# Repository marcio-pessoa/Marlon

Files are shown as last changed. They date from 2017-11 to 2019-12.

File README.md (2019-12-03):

# Marlon Mark I - 3D Printer

## Introduction

Marlon is a Marlin firmware based 3D Printer. It uses RepRap concept with RAMPS.

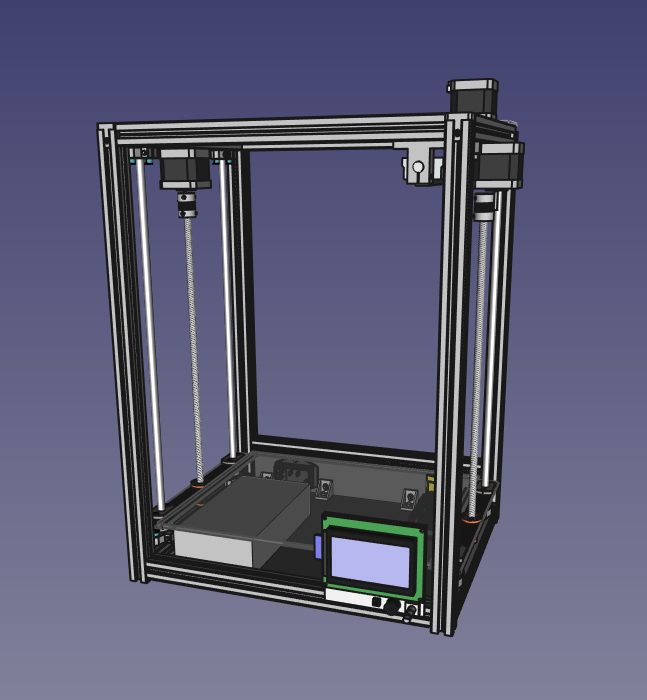
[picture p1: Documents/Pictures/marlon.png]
Marlon


## Cloning
```
git clone --recurse-submodules https://github.com/marcio-pessoa/Marlon.git
```

<!---
Work area:

Width: ??? mm
Height: ??? mm
Depth: ??? mm

## Videos
Watch this projects videos on [YouTube Playlist].
--->

## Changes
All notable changes to this project will be documented in this [Change log](CHANGELOG.md).

## Mechanics
This project uses an original mech made from scratch with the following goals:
- Reliable
- Precise
- Robust
- Well done
- Almost cheap, but very beautiful

Check out [Mechanics](Mechanics/README.md) design to know more.

## Electronics
Arduino, RAMPS and Full Graphic Smart Controller are used to [Electronics](Electronics/README.md) control system.

## Firmware
Marlin is my [Firmware](Firmware/README.md)! :-)

## Software
A lot of softwares can be used to draw 3D objects, slice, convert to G-code and print. Here are [some recommended softwares](Software/README.md).

## BOM - Bill of materials
If you want to build your own, take a look at [Bill of materials](BOM.md).

---

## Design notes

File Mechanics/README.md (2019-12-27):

# Marlon Mark I - 3D Printer

[Main page]

## Mechanics

### Frame
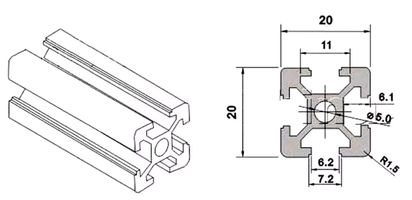
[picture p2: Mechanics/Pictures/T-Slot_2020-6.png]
T-Slot 2020-6


Technical specifications:
- Frame type: T-Slot 2020-6
- Width: 337 mm
- Height: 445 mm
- Depth: 287 mm

#### Hinges
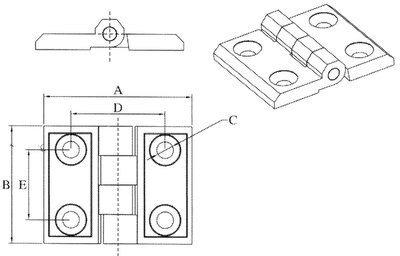
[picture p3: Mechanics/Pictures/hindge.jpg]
T-Slot 2020 Hinge


T-Slot 2020 Hinge

Technical specifications:
- Frame type: T-Slot 2020-6
- A:  mm
- B:  mm
- C:  mm
- D:  mm
- E:  mm

#### Round Roll T-Nut for T-slot 2020

##### M3
Technical specifications:
- Material: Nickel Plated
- Shaft: 3mm

##### M4
Technical specifications:
- Material: Nickel Plated
- Shaft: 4mm

##### M5
Technical specifications:
- Material: Nickel Plated
- Shaft: 5mm

### CoreXY
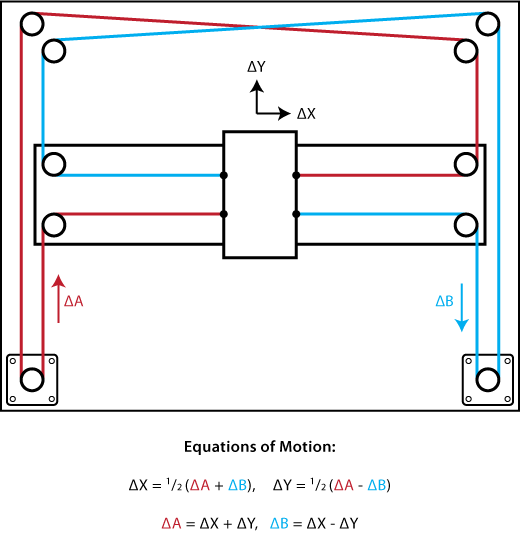
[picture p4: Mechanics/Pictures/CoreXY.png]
CoreXY


The [CoreXY] is a open source two-axis linear motion implementation developed at MIT Media Lab.

Overall, it delivers the same benefit of the H-bot, a light moving platform, by keeping both motors fixed to the frame. Furthermore, by crossing the belt, the unwanted torque vectors of H-bot model are eliminated.

#### SC8LUU
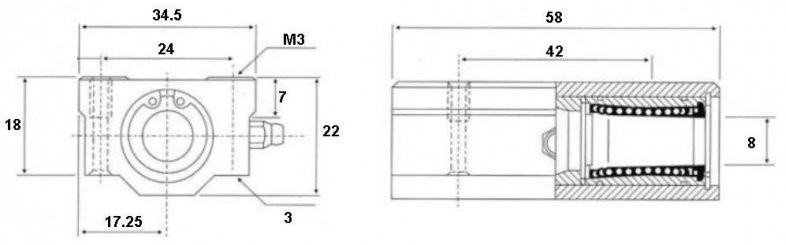
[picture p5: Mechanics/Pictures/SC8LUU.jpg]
SC8LUU


Technical specifications:

#### Linear rod
Technical specifications:
- Diameter: 8 mm
- Lenght: 300 mm
- Material: Carbon Steel

#### Pulley
Technical specifications:
- Timing: 20T
- Bore: 5mm
- Belt: GT2 6 mm

#### Belt
Technical specifications:
- Standard: GT2
- Pinch: 2 mm
- Wide: 6 mm
- Lenght: <span style="color:#F00">???</span> mm

### Elevator (z axis)

#### Base
Technical specifications:
- Material: Celeron

#### LMH8UU
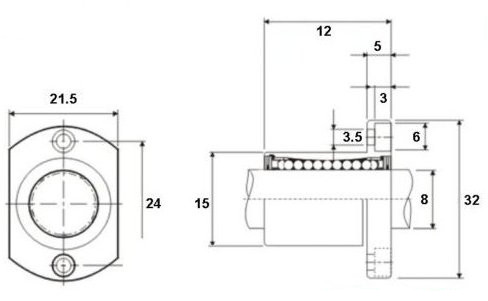
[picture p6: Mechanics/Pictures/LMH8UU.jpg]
LMH8UU


#### SHF
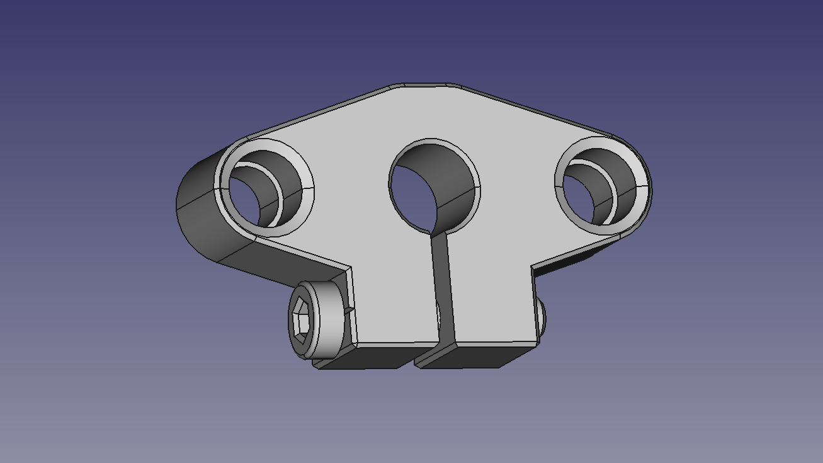
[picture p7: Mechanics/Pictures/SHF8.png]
SHF


Technical specifications:

#### Shaft coupler
Technical specifications:
- Diameter: 19 mm
- Lenght: 25 mm
- Material: Aluminium
- Net weight: 16 g
- Shaft: 5 -> 8 mm

#### Threaded rod
Technical specifications:
- Material: 304 Stainless Steel
- Diameter: 8 mm
- Pitch: 2 mm
- Lead: 4
- Length: 400 mm

#### T8
Technical specifications:
- Material: Brass
- Big nut diameter: 30mm
- Thickness: 5mm
- Small nut diameter: 16mm
- Feature: anti-backlash

#### Linear rail
Technical specifications:
- Diameter: 8 mm
- Lenght: 400 mm
- Material: Carbon Steel

[Main page]

---

[Celeron TechSpecs]: dados-tecnicos-celeron.pdf
[Main page]: ../README.md
[CoreXY]: http://corexy.com/

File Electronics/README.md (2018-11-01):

# Marlon Mark I - 3D Printer

[Main page]

## Electronics

### Power
Technical specifications:
https://www.stayonline.com/5-15-c13-10-amp-power-cords.aspx

- N: neutro (black)
- F: fase (white)
- T: ground (green)

#### Power connector

             T        
          +------+    
         /   ▉▉   \   
        +          +  
        | ▉▉    ▉▉ |  
        +----------+  
          F      N    

Technical specifications:
- Standard: IEC 60320
- Coupler: C13

#### Power supply
Technical specifications:
- Model: PMC-12V150W1BA
- Technology: Switching power supply
- Input:
  - Voltage: 100 ~ 240 VAC
  - Amperage: 2 A
  - Frequency: 50 ~ 60 Hz
  - Power: 150 W
- Output 1: 
  - Voltage: 12 VDC
  - Amperage: 12.6 A

### Arduino
Technical specifications:
- Model: [Arduino Mega 2560]

#### Diagram
                                 .-----.                                        
    .----[PWR]-------------------| USB |--.                                     
    |                            '-----'  |                                     
    |           GND/RST2  [ ] [ ]         |                                     
    |         MOSI2/SCK2  [ ] [ ]  SCL[ ] |   D0                                
    |            5V/MISO2 [ ] [ ]  SDA[ ] |   D1                                
    |                             AREF[ ] |                                     
    |                              GND[ ] |                                     
    | [ ]NC                     SCK/13[ ]~|   B7                                
    | [ ]v.ref                 MISO/12[ ]~|   B6                                
    | [ ]RST                   MOSI/11[ ]~|   B5                                
    | [ ]3V3      +----------+      10[ ]~|   B4                                
    | [ ]5v       | ARDUINO  |       9[ ]~|   H6                                
    | [ ]GND      |   MEGA   |       8[ ]~|   H5                                
    | [ ]GND      +----------+            |                                     
    | [ ]Vin                         7[ ]~|   H4                                
    |                                6[ ]~|   H3                                
    | [ ]A0                          5[ ]~|   E3                                
    | [ ]A1                          4[ ]~|   G5                                
    | [ ]A2                     INT5/3[ ]~|   E5                                
    | [ ]A3                     INT4/2[ ]~|   E4                                
    | [ ]A4                       TX>1[ ]~|   E1                                
    | [ ]A5                       RX<0[ ]~|   E0                                
    | [ ]A6                               |                                     
    | [ ]A7                     TX3/14[ ] |   J1                                
    |                           RX3/15[ ] |   J0                                
    | [ ]A8                     TX2/16[ ] |   H1                                
    | [ ]A9                     RX2/17[ ] |   H0                                
    | [ ]A10               TX1/INT3/18[ ] |   D3                                
    | [ ]A11               RX1/INT2/19[ ] |   D2                                
    | [ ]A12           I2C-SDA/INT1/20[ ] |   D1                                
    | [ ]A13           I2C-SCL/INT0/21[ ] |   D0                                
    | [ ]A14                              |                                     
    | [ ]A15                              |   PORTS                             
    |                RST SCK MISO         |    22=A0  23=A1                     
    |         ICSP   [ ] [ ] [ ]          |    24=A2  25=A3                     
    |                [ ] [ ] [ ]          |    26=A4  27=A5                     
    |                GND MOSI 5V          |    28=A6  29=A7                     
    | G                                   |    30=C7  31=C6                     
    | N 5 5 4 4 4 4 4 3 3 3 3 3 2 2 2 2 5 |    32=C5  33=C4                     
    | D 2 0 8 6 4 2 0 8 6 4 2 0 8 6 4 2 V |    34=C3  35=C2                     
    |         ~ ~                         |    36=C1  37=C0                     
    | @ # # # # # # # # # # # # # # # # @ |    38=D7  39=G2                     
    | @ # # # # # # # # # # # # # # # # @ |    40=G1  41=G0                     
    |           ~                         |    42=L7  43=L6                     
    | G 5 5 4 4 4 4 4 3 3 3 3 3 2 2 2 2 5 |    44=L5  45=L4                     
    | N 3 1 9 7 5 3 1 9 7 5 3 1 9 7 5 3 V |    46=L3  47=L2                     
    | D                                   |    48=L1  49=L0    SPI:             
    |                                     |    50=B3  51=B2     50=MISO 51=MOSI
    |     2560                            |    52=B1  53=B0     52=SCK  53=SS   
    '--.                         .--------'                                     
        \_______________________/                                               

Diagram by: http://busyducks.com/ascii-art-arduinos

#### Pin designation
 id | pin |   type    | direction |               description                
----|-----|-----------|-----------|--------------------------------------------
  0 |   0 | -         | -         | -                                        
  1 |   1 | -         | -         | -                                        
  2 |   2 | -         | -         | X_MAX_PIN                                
  3 |   3 | -         | -         | X_MIN_PIN                                
  4 |   4 | -         | -         | -                                        
  5 |   5 | -         | -         | -                                        
  6 |   6 | -         | -         | -                                        
  7 |   7 | -         | -         | -                                        
  8 |   8 | -         | -         | HEATER_1_PIN                             
  9 |   9 | -         | -         | FAN_PIN                                  
 10 |  10 | -         | -         | HEATER_0_PIN                             
 11 |  11 | -         | -         | -                                        
 12 |  12 | -         | -         | PS_ON_PIN                                
 13 |  13 | -         | -         | LED_PIN                                  
 14 |  14 | -         | -         | Y_MIN_PIN                                
 15 |  15 | -         | -         | Y_MAX_PIN                                
 16 |  16 | -         | -         | -                                        
 17 |  17 | -         | -         | -                                        
 18 |  18 | -         | -         | Z_MIN_PIN                                
 19 |   4 | -         | -         | Z_MAX_PIN                                
 20 |  20 | -         | -         | -                                        
 21 |  21 | -         | -         | -                                        
 22 |  22 | -         | -         | -                                        
 23 |  23 | -         | -         | -                                        
 24 |  24 | -         | -         | E_ENABLE_PIN                             
 25 |  25 | -         | -         | -                                        
 26 |  26 | -         | -         | E_STEP_PIN                               
 27 |  27 | -         | -         | -                                        
 28 |  28 | -         | -         | E_DIR_PIN                                
 29 |  29 | -         | -         | -                                        
 30 |  30 | -         | -         | -                                        
 31 |  31 | -         | -         | -                                        
 32 |  32 | -         | -         | -                                        
 33 |  33 | -         | -         | -                                        
 34 |  34 | -         | -         | -                                        
 35 |  35 | -         | -         | -                                        
 36 |  36 | -         | -         | -                                        
 37 |  37 | -         | -         | -                                        
 38 |  38 | -         | -         | X_ENABLE_PIN                             
 39 |  39 | -         | -         | -                                        
 40 |  40 | -         | -         | -                                        
 41 |  41 | -         | -         | -                                        
 42 |  42 | -         | -         | -                                        
 43 |  43 | -         | -         | -                                        
 44 |  44 | -         | -         | -                                        
 45 |  45 | -         | -         | -                                        
 46 |  46 | -         | -         | Z_STEP_PIN                               
 47 |  47 | -         | -         | -                                        
 48 |  48 | -         | -         | Z_DIR_PIN                                
 49 |  49 | -         | -         | -                                        
 50 |  50 | -         | -         | -                                        
 51 |  51 | -         | -         | -                                        
 52 |  52 | -         | -         | -                                        
 53 |  53 | -         | -         | SDSS                                     
 54 |   0 | -         | -         | X_STEP_PIN                               
 55 |   1 | -         | -         | X_DIR_PIN                                
 56 |   2 | -         | -         | Y_ENABLE_PIN                             
 57 |   3 | -         | -         | -                                        
 58 |   4 | -         | -         | -                                        
 59 |   5 | -         | -         | -                                        
 60 |   6 | -         | -         | Y_STEP_PIN                               
 61 |   7 | -         | -         | Y_DIR_PIN                                
 62 |   8 | -         | -         | Z_ENABLE_PIN                             
 63 |   9 | -         | -         | -                                        
 64 |  10 | -         | -         | -                                        
 65 |  11 | -         | -         | -                                        
 66 |  12 | -         | -         | -                                        
 67 |  13 | -         | -         | TEMP_0_PIN                               
 68 |  14 | -         | -         | TEMP_1_PIN                               
 69 |  15 | -         | -         | -                                        

### RAMPS
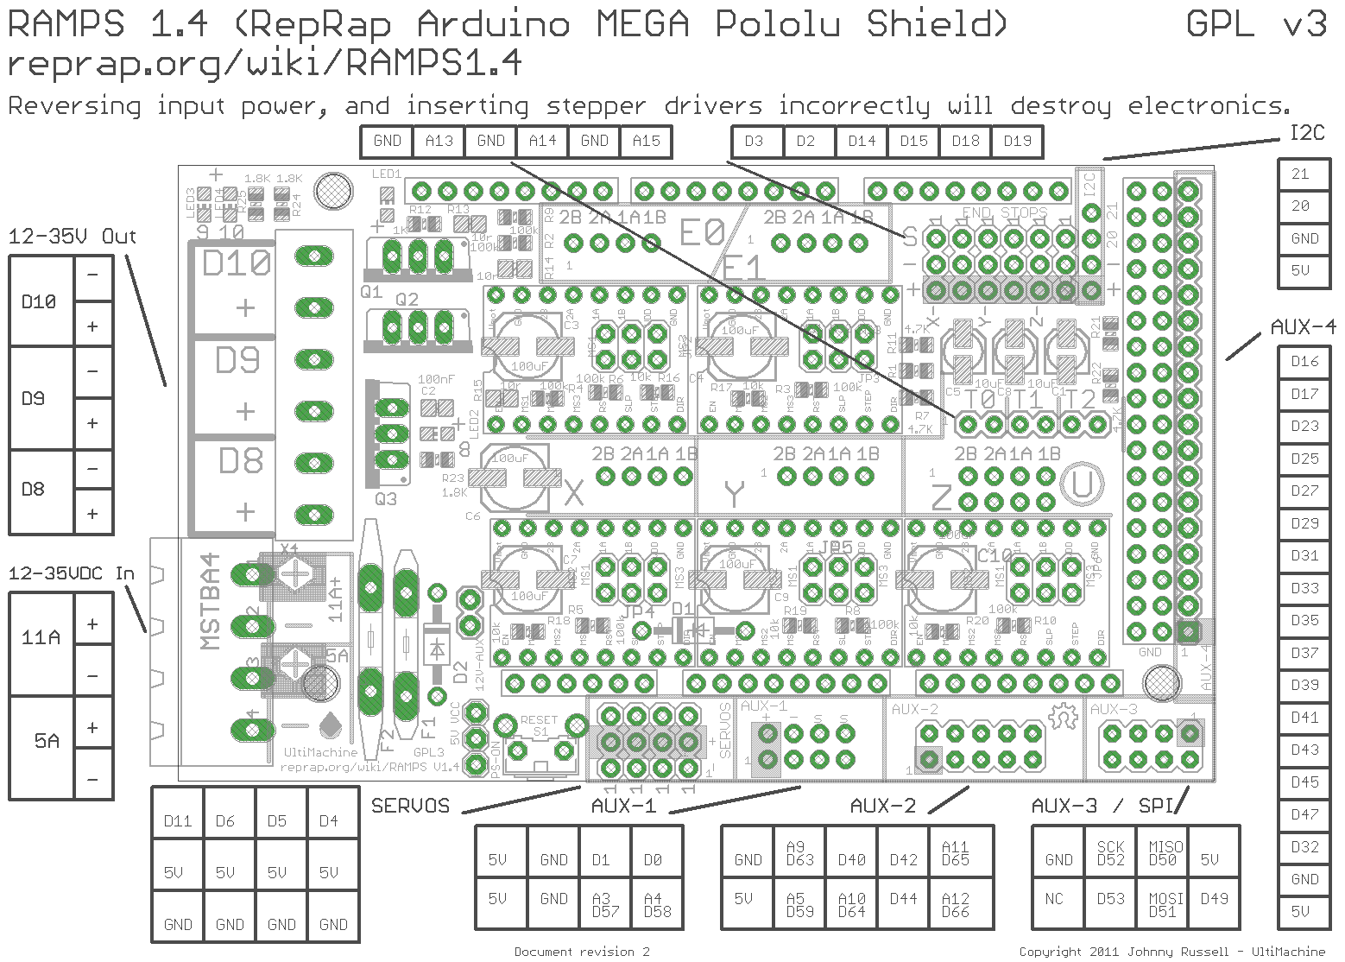
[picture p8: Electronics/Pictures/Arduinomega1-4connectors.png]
RAMPS 1.4


> RepRap Arduino Mega Pololu Shield, or RAMPS for short. It is designed to fit the entire electronics needed for a RepRap in one small package for low cost. RAMPS interfaces an Arduino Mega with the powerful Arduino MEGA platform and has plenty room for expansion. The modular design includes plug in stepper drivers and extruder control electronics on an Arduino MEGA shield for easy service, part replacement, upgrade-ability and expansion. Additionally, a number of Arduino expansion boards can be added to the system as long as the main RAMPS board is kept to the top of the stack.
>
> -- From: [RAMPS]

Technical specifications:
- Version: 1.4
- License: GPL

### Display
Technical specifications:
- Model: [Full Graphic Smart Controller]
- Resolution: 128 x 64 pixels
- Technology: LCD
- License: GPL
- Author: RepRapDiscount.com

### Stepper drivers
Technical specifications:
- Model: A4988

Each driver has and heat sink to 

RAMPS has 3 jumpers to configure each axes resolution.
That can be set to configure the motor microstepping.

#### Resolution configuration

##### Pololu A4988
 M0   | M1   | M2   | Microstep resolution
------|------|------|-----------------------
 Low  | Low  | Low  | Full step
 High | Low  | Low  | Half step
 Low  | High | Low  | Quarter step
 High | High | Low  | Eighth step
 High | High | High | Sixteenth step

##### Pololu DRV8825
 M0   | M1   | M2   | Microstep resolution
------|------|------|-----------------------
 Low  | Low  | Low  | Full step
 High | Low  | Low  | Half step
 Low  | High | Low  | 1/4 step
 High | High | Low  | 1/8 step
 Low  | Low  | High | 1/16 step
 High | Low  | High | 1/32 step
 Low  | High | High | 1/32 step
 High | High | High | 1/32 step

### Stepper motor
Technical specifications:
- Model: 42BYGHM809
- Holding Torque: 48 N·cm
- Rated voltage: 3.06 V
- Shaft: Ø 5 mm no flat
- Step angle: 0.9 degree
- Motor length: 48 mm
- Rated current: 1.7 A/phase
- Inductance: 2.8 mH
- Frame Size: NEMA17
- Step Angle:                    0.9 degree
- Wires: 4
- Weight: 0.34 kg
- Length: 48 mm
- Motor shaft : 5mm
- Front shaft length: 20mm

<!---
- Voltage: 2.8V
- Resistance: 1.65Ohm/phase
- Inductance: 4.0mH/phase
- Holding torque: 4200g.cm 60oz-in
- Rotor inertia: 68g-cm2
- Detent torque: 0.22g-cm
--->

Stepper motor [reference](http://reprap.org/wiki/NEMA_17_Stepper_motor).

### Hot bed

### Endstop sensor
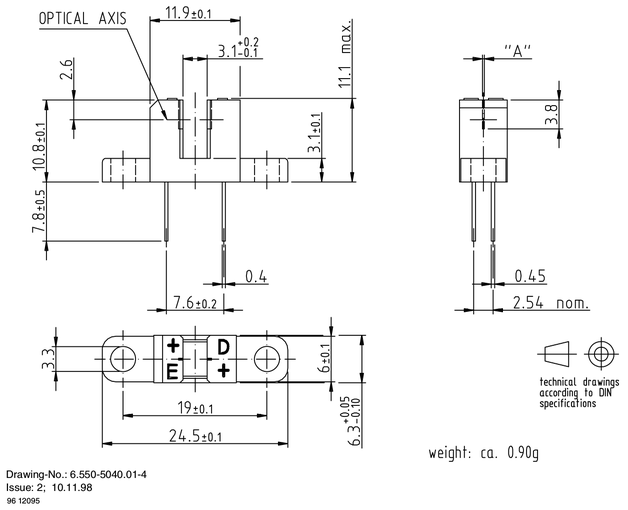
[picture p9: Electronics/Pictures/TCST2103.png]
TCST2103


Technical specifications:
- Type: Optical
- Model: [TCST2103](../Documents/TCST2103.pdf)

### Fans
Technical specifications:
- Type: Brushless
- Feature: Noiseless
- Size: 50 x 50 x 10 mm
- Voltage: 12 VDC
- Amperage: 0.12 A

[Main page]

---

[Main page]: ../README.md
[RAMPS]: http://reprap.org/wiki/RAMPS
[Arduino Mega 2560]: https://store.arduino.cc/usa/arduino-mega-2560-rev3
[Full Graphic Smart Controller]: https://reprap.org/wiki/RepRapDiscount_Full_Graphic_Smart_Controller

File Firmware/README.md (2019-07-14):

# Marlon Mark I - 3D Printer

[Main page]

## Firmware

### Marlin
> "Marlin is an open source firmware for the RepRap family of replicating rapid prototypers — popularly known as “3D printers.” It was derived from Sprinter and grbl, and became a standalone open source project on August 12, 2011 with its Github release. Marlin is licensed under the GPLv3 and is free for all applications.
>
> From the start Marlin was built by and for RepRap enthusiasts to be a straightforward, reliable, and adaptable printer driver that “just works.” As a testament to its quality, Marlin is used by several respected commercial 3D printers. Ultimaker, Printrbot, AlephObjects (Lulzbot), and Prusa Research are just a few of the vendors who ship a variant of Marlin.
>
> One key to Marlin’s popularity is that it runs on inexpensive 8-bit Atmel AVR micro-controllers. These chips are at the center of the popular open source Arduino/Genuino platform. The reference platform for Marlin is an Arduino Mega2560 with RAMPS 1.4.
>
> As a community product, Marlin aims to be adaptable to as many boards and configurations as possible. We want it to be configurable, customizable, extensible, and economical for hobbyists and vendors alike. A Marlin build can be very small, for use on a headless printer with only modest hardware. Features are enabled as-needed to adapt Marlin to added components."
>
> As a community product, Marlin aims to be adaptable to as many boards and configurations as possible. We want it to be configurable, customizable, extensible, and economical for hobbyists and vendors alike. A Marlin build can be very small, for use on a headless printer with only modest hardware. Features are enabled as-needed to adapt Marlin to added components."
>
> -- From: [Marlin web page] and [Marlin GitHub]

#### Configuring
[Marlin Configuring]

#### G-code
[Marlin G-code]

##### Fan control
M106: On
M107: Off

#### Calibration

[Main page]

---

[Main page]: ../README.md
[Marlin]: http://marlinfw.org/
[Marlin on GitHub]: https://github.com/MarlinFirmware/Marlin
[Marlin G-code]: http://marlinfw.org/meta/gcode/
[Marlin Configuring]: http://marlinfw.org/docs/configuration/configuration.html
[Marlin web page]: http://marlinfw.org/
[Marlin GitHub]: https://github.com/MarlinFirmware/Marlin

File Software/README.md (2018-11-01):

# Marlon Mark I - 3D Printer

[Main page]

## Software

### Draw

#### FreeCAD
> "FreeCAD is a general purpose feature-based, parametric 3D modeler for CAD, MCAD, CAx, CAE and PLM, aimed directly at mechanical engineering and product design but also fits a wider range of uses in engineering, such as architecture or other engineering specialties. It is 100% Open Source (LGPL2+ license) and extremely modular, allowing for very advanced extension and customization."
>
> -- From: [FreeCAD GitHub]

- [FreeCAD website](http://www.freecadweb.org)

#### OpenSCAD
> "OpenSCAD is a software for creating solid 3D CAD objects. It is free software and available for Linux/UNIX, MS Windows and Mac OS X."
>
> "Unlike most free software for creating 3D models (such as the famous application Blender), OpenSCAD focuses on the CAD aspects rather than the artistic aspects of 3D modeling. Thus this might be the application you are looking for when you are planning to create 3D models of machine parts but probably not the tool for creating computer-animated movies."
>
> "OpenSCAD is not an interactive modeler. Instead it is more like a 3D-compiler that reads a script file that describes the object and renders the 3D model from this script file (see examples below). This gives you, the designer, complete control over the modeling process and enables you to easily change any step in the modeling process or make designs that are defined by configurable parameters."
>
> "OpenSCAD provides two main modeling techniques: First there is constructive solid geometry (aka CSG) and second there is extrusion of 2D outlines. As the data exchange format for these 2D outlines Autocad DXF files are used. In addition to 2D paths for extrusion it is also possible to read design parameters from DXF files. Besides DXF files OpenSCAD can read and create 3D models in the STL and OFF file formats."
>
> -- From: [OpenSCAD website]

- [OpenSCAD GitHub]

### Slice

#### Slic3r
> "Slic3r is mainly a toolpath generator for 3D printers: it reads 3D models (STL, OBJ, AMF, 3MF) and it converts them into G-code instructions for 3D printers. But it does much more than that..."
>
> -- From: [Slic3r GitHub]

- [Slic3r website]
- [Slic3r manual]

### Print

#### OctoPrint
> "OctoPrint provides a snappy web interface for controlling consumer 3D printers. It is Free Software and released under the GNU Affero General Public License V3."
>
> -- From: [OctoPrint GitHub]

- [OctoPrint website]

[Main page]

---

[Main page]: ../README.md
[FreeCAD website]: https://www.freecadweb.org/
[FreeCAD GitHub]: https://github.com/FreeCAD/FreeCAD
[OpenSCAD website]: http://www.openscad.org/
[OpenSCAD GitHub]: https://github.com/openscad/openscad/
[Slic3r website]: http://slic3r.org/
[Slic3r manual]: http://manual.slic3r.org/advanced/command-line
[Slic3r GitHub]: https://github.com/slic3r/Slic3r
[OctoPrint website]: https://octoprint.org/
[OctoPrint GitHub]: https://github.com/foosel/OctoPrint

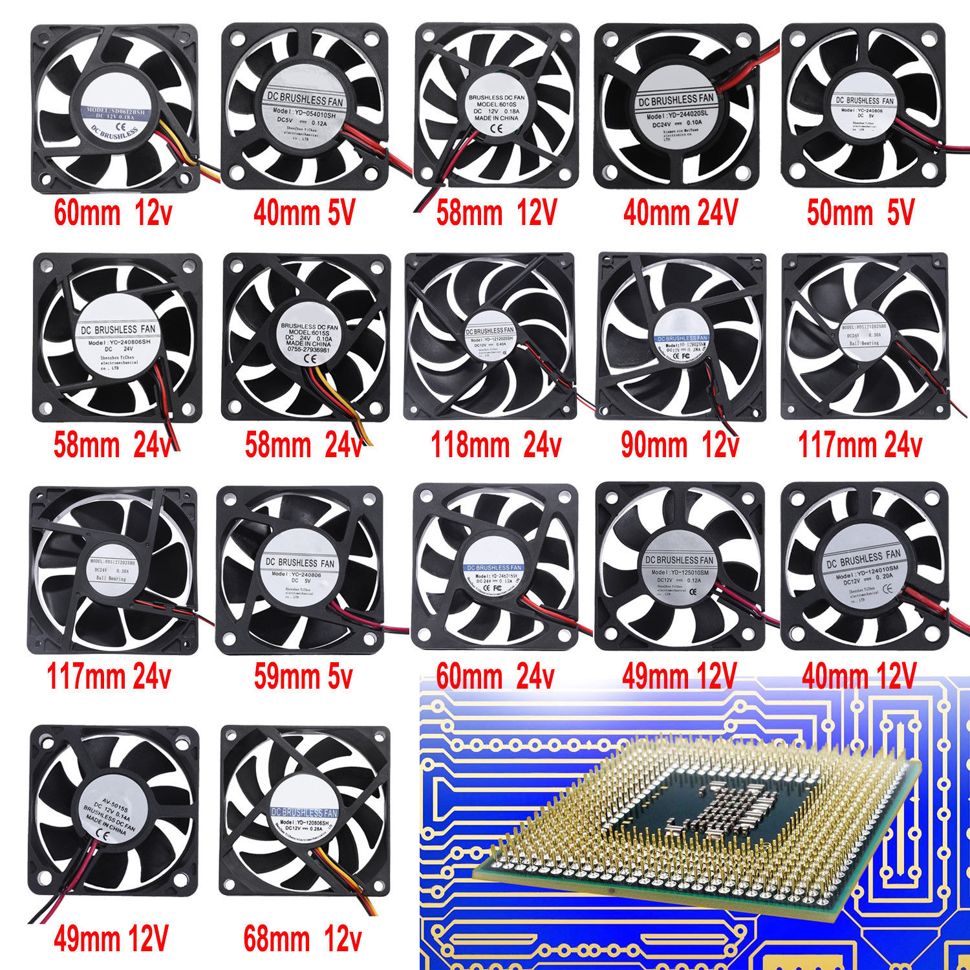
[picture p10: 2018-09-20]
Electronics/Pictures/s-l1600aaaa.jpg

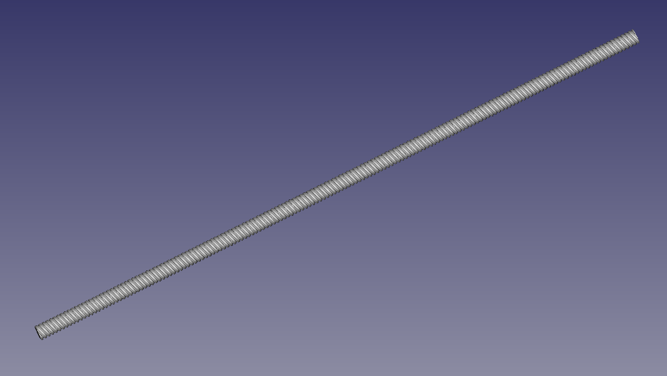
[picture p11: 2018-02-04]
Electronics/Pictures/Threaded.png

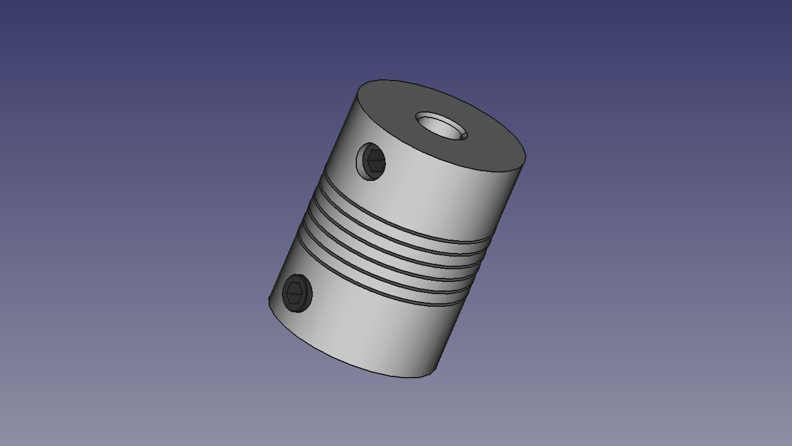
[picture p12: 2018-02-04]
Mechanics/Pictures/Shaft_coupler.png

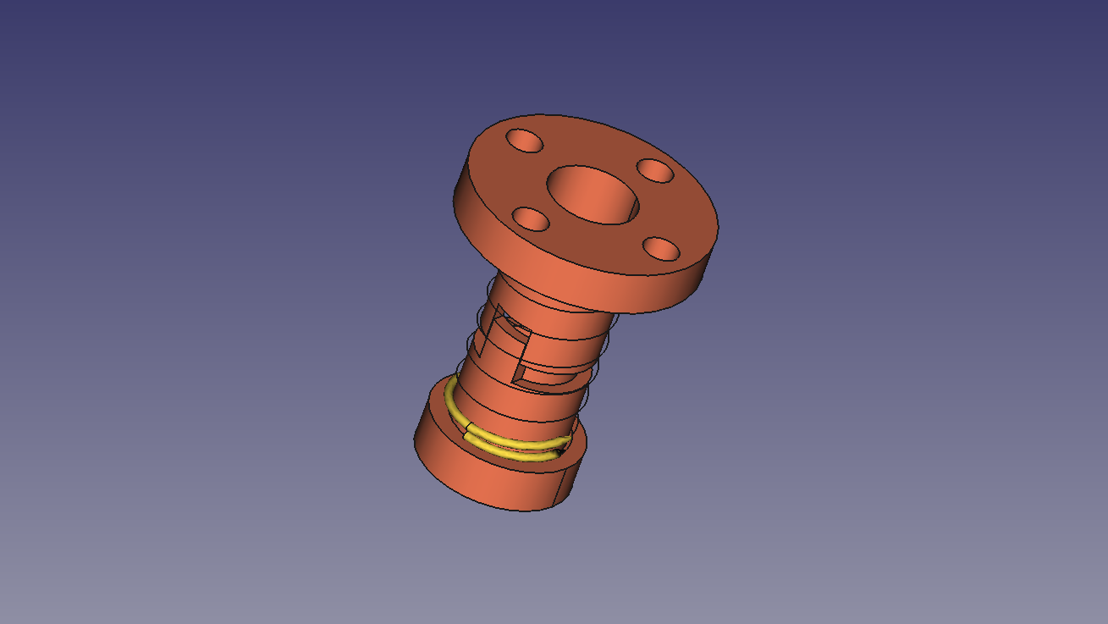
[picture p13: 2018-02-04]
Mechanics/Pictures/T8.png

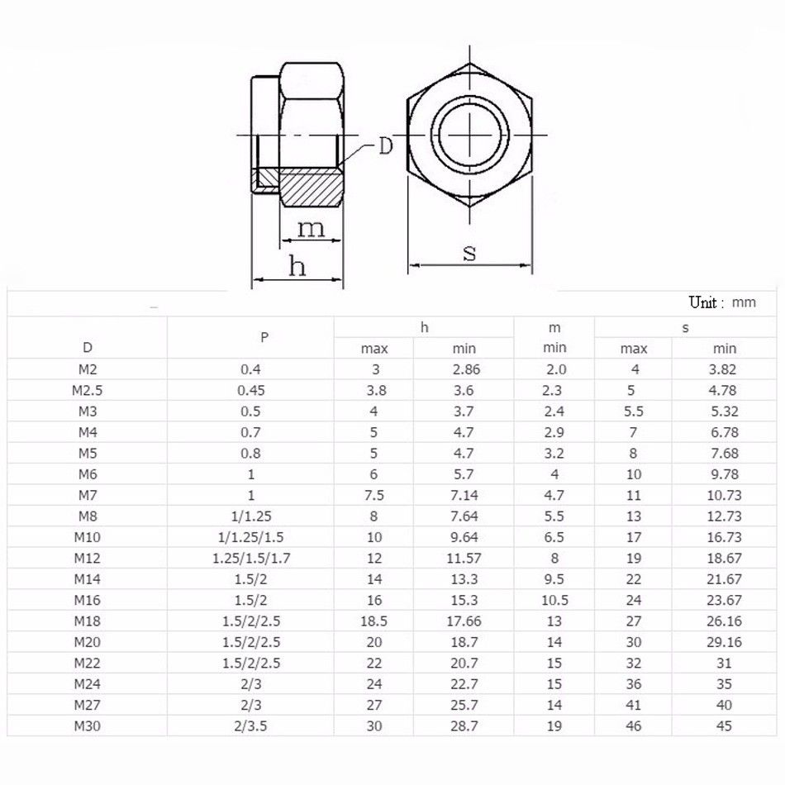
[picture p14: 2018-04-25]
Mechanics/Pictures/s-l1600a.jpg

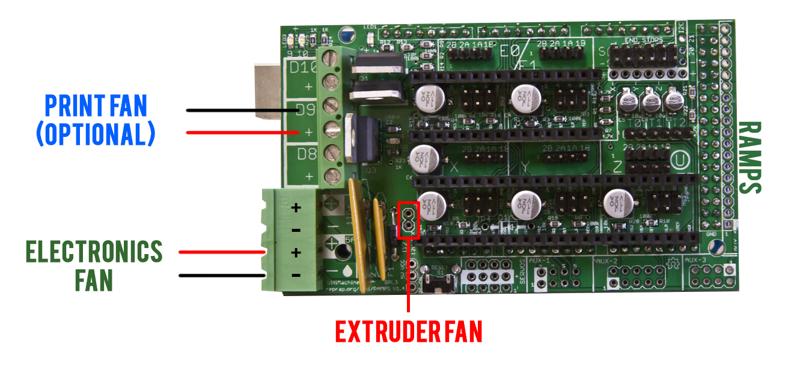
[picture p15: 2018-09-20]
Electronics/Pictures/Cablage_Ventilateurs-EN.jpg

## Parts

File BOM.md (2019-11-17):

# BOM
Marlon Mark I - 3D Printer, Bill of materials

## Purchased
| Quant | Description | ID | Bought | Delivered  | Unit | Charge | Taxes | Cost |
|---|---|---|---|---|---|---|---|---|
| 1 | Frame | 252822719913 | 2017-08-19 | 2017-10-11 | each |  99.00 | 69.07 | 168.07 |
| 1 | RAMPS | 252297680208 | 2016-02-28 | 2016-mm-dd | each |  28.98 |  1.85 |  30.83 |
| 1 | Arduino_Mega | 252297680208 | 2016-02-28 | 2016-mm-dd | each | 0.00 |  0.00 | 0.00 |
| 1 | USB_cable | 252297680208 | 2016-02-28 | 2016-mm-dd | each | 0.00 |  0.00 | 0.00 |
| 5 | Stepper_drivers | 252297680208 | 2016-02-28 | 2016-mm-dd | each | 0.00 |  0.00 | 0.00 |
| 5 | Drivers_Heat_sink | 252297680208 | 2016-02-28 | 2016-mm-dd | each | 0.00 |  0.00 | 0.00 |
| 1 | Display | 272150628431 | 2016-03-08 | 2016-mm-dd | each | 9.22 |  0.59 | 9.81 |
| 1 | Display_cable | 272150628431 | 2016-03-08 | 2016-mm-dd | each | 0.00 |  0.00 | 0.00 |
| 1 | PSU_12VDC/30A | - | 2015-03-28 | 2015-03-28 | each | 0.00 |  0.00 | 0.00 |
| 1 | PSU_AC_connector | 172193375231 | 2016-10-09 | 2016-mm-dd | each | 1.99 |  0.13 | 2.12 |
| 1 | Power_cable | - | 2014-mm-dd | 2014-mm-dd | each | 1.99 |  0.13 | 2.12 |
| 1 | Display_knob | 221939971151 | 2016-04-24 | 2016-mm-dd | each | 1.29 |  0.07 | 1.36 |
| 1 | Power_switch | 221989151099 | 2016-02-25 | 2016-mm-dd | each | 2.48 |  0.16 | 2.64 |
| 4 | Adhesive_Feet | - | 2014-mm-dd | 2014-mm-dd | each | 0.00 |  0.00 | 0.00 |
| 7 | Optical_Endstop | 381842310412 | 2016-12-22 | 2017-05-18 | each | 5.62 |  0.36 | 5.98 |
| 1 | Black_Adhesive_cover | - | 2018-04-06 | 2018-04-06 | m | 2.14 |  0.00 | 2.14 |
| 50 | T-Slot_2020_Nut_M5 | 112377337972 | 2017-10-14 | 2017-12-dd | each | 8.54 |  0.53 | 9.07 |
| 20 | T-Slot_2020_Nut_M4 | 112377337972 | 2017-10-14 | 2017-12-dd | each | 5.22 |  0.32 | 5.54 |
| 20 | T-Slot_2020_Nut_M3 | 112377337972 | 2017-10-14 | 2017-12-dd | each | 5.22 |  0.32 | 5.54 |
| 2 | Shaft_coupler | 292335491058 | 2017-11-23 | 2018-01-26 | each | 1.25 |  0.08 | 1.33 |
| 4 | LMH8UU | 112098366186 | 2017-10-14 | 2018-04-03 | each | 5.58 |  0.36 | 5.94 |
| 1 | Back_panel_304x46 | - | 2018-03-08 | 2018-03-08 | each | 0.00 |  0.00 | 0.00 |
| 1 | Bottom_panel_334x280 | - | 2018-03-08 | 2018-03-08 | each |  52.00 |  0.00 |  52.00 |
| 2 | GT2_20T_Bore | 292316604447 | 2017-11-08 | 2018-04-07 | each | 1.00 |  0.05 | 1.05 |
| 4 | Washers_M4 | 172371032208 | 2017-08-15 | 2018-03-26 | each | 0.09 |  0.01 | 0.10 |
| 4 | SC8LUU | 272351135444 | 2017-10-14 | 2018-04-09 | each |  20.50 |  1.31 |  21.81 |
| 12 | SHF8 | 222702698960 | 2017-11-05 | 2018-04-11 | each |  17.76 |  1.12 |  18.88 |
| 2 | Aluminium_Hinge | 302591989386 | 2018-01-05 | 2018-06-12 | each | 2.00 |  0.13 | 2.13 |
| 4 | Screw_M3x6mm | 232313079440 | 2018-03-21 | 2018-06-04 | each | 0.09 |  0.01 | 0.10 |
| 10 | Screw_M3x10mm_flat | 222418404772 | 2018-06-24 | 2018-07-23 | each | 1.35 |  0.09 | 1.47 |
| 3 | T-slot_90_corner | 131977551173 | 2016-11-04 | 2016-mm-dd | each | 0.75 |  0.05 | 0.80 |
| 2 | Threaded_rod_8x400mm | 272804811413 | 2018-08-24 | 2018-09-27 | each |  13.43 |  0.86 |  14.29 |
| 2 | TR8 | 272804811413 | 2018-08-24 | 2018-09-27 | each | 0.00 |  0.00 | 0.00 |
| 50 | Screw_M4x8mm_flat | 223120558333 | 2018-08-31 | 2018-10-09 | each | 2.66 |  0.17 | 2.83 |
| 2 | Stepper_2BYGHM809 | 151226573075 | 2018-10-08 | 2018-10-30 | each |  32.96 |  2.10 |  35.06 |
| 4 | Linear_rod_8x400mm | 292628042096 | 2018-09-30 | 2018-11-09 | each |  17.09 |  1.08 |  18.17 |
| 4 | Linear_rod_8x330mm | 282779129630 | 2018-10-12 | pending | each | 7.89 | | |
| 2 | Stepper_2BYGHM809 | 151226573075 | 2018-10-08 | 2018-mm-dd | each |  32.96 |  2.10 |  35.06 |
| 4 | SK8 | 272564840128 | 2019-03-31 | pending | each | 3.96 | | |
| 2 | Fan_50x50x10 | pending | pending | pending | each | 0.00 |  0.00 | 0.00 |
| ? | GT2_belt | pending | pending | pending | cm | 0.00 |  0.00 | 0.00 |
| 1 | Extruder_Carriage | 382749311851 | 2019-03-10 | 2019-03-dd | cm |  22.38 |  1.48 |  23.86 |
| 1 | Hot_bed | 302931840885 | 2018-12-20 | 2019-03-dd | cm |  32.93 |  5.97 |  38.90 |
| 8 | Screw_hex_M5_10mm | 182973693071 | 2019-05-04 | pending | each | 2.38 |  0.14 | 2.52 |
| 2 | SK8 | 232670339051 | 2018-11-27 | 2019-mm-dd | each | 4.25 |  0.26 | 4.51 |
| 2 | SK6 | 182971368756 | 2017-07-01 | 2019-09-dd | each | 6.21 |  0.40 | 6.61 |
| 1 | Celeron_360x241x2mm  | pending | pending | pending | each | | | |

Currency: USD<br/>
International IOF: 6.38%<br/>
Domestic IOF: 0.38%

Total cost: $532.64

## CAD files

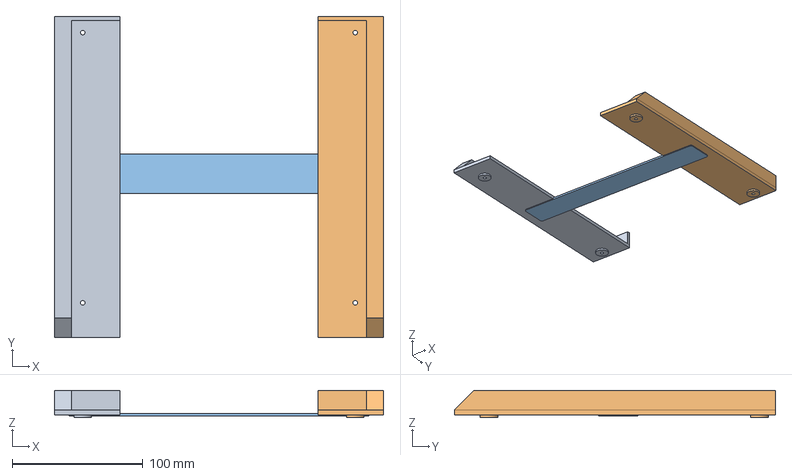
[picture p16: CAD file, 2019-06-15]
Mechanics/Anet_A8_removable_heat_bed.FCStd
252.0 x 246.0 x 20.7 mm
Cut003 (Mirror #1)

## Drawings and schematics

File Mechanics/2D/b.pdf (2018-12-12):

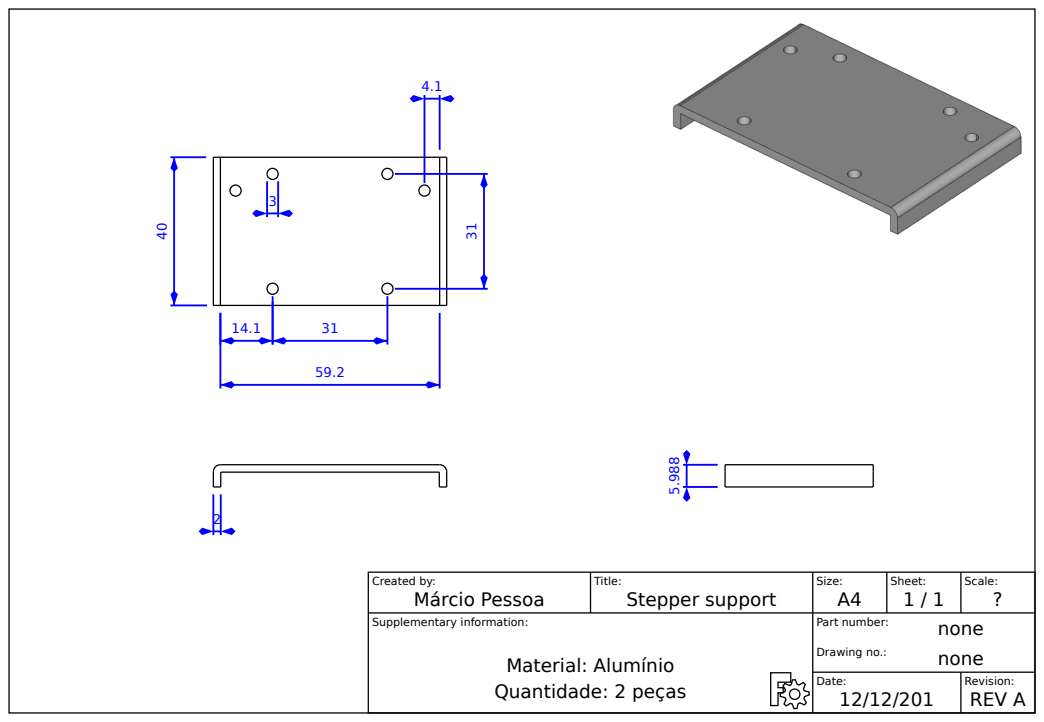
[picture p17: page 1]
Created by:; Title:; Supplementary information:; Size:; Sheet:; Scale:; Part number:; Drawing no.:; Date:; Revision:; Márcio Pessoa; Stepper support; Material: Alumínio Quantidade: 2 peças; none none; REV A

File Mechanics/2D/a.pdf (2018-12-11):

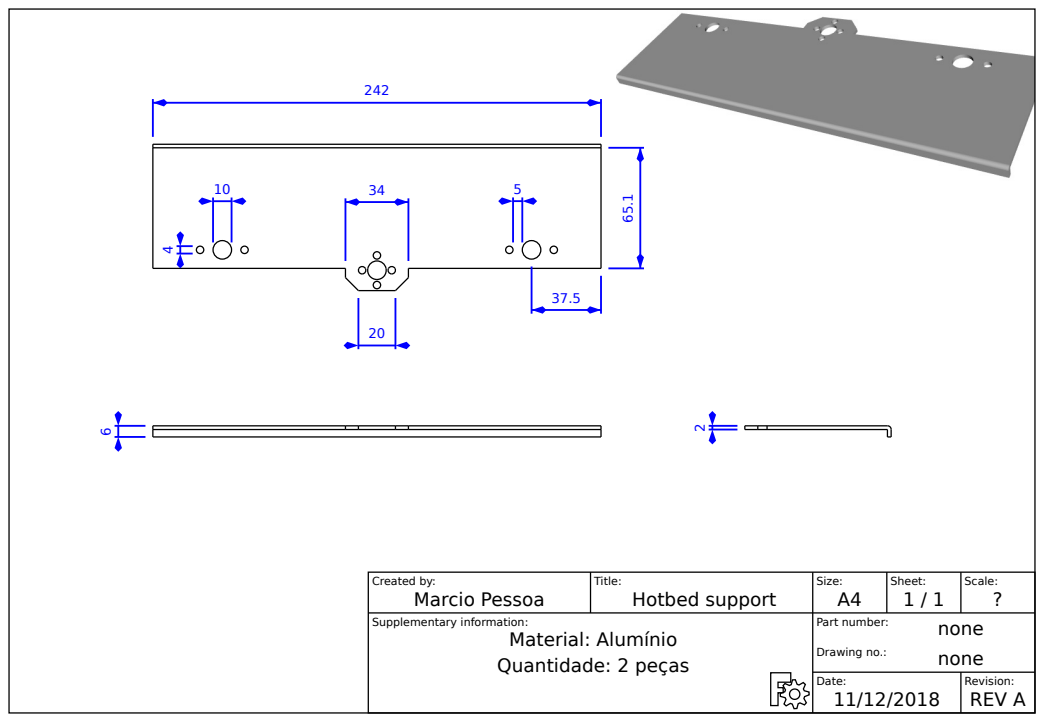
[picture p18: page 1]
Created by:; Title:; Supplementary information:; Size:; Sheet:; Scale:; Part number:; Drawing no.:; Date:; Revision:; Marcio Pessoa; Hotbed support; Material: Alumínio Quantidade: 2 peças; none none; REV A

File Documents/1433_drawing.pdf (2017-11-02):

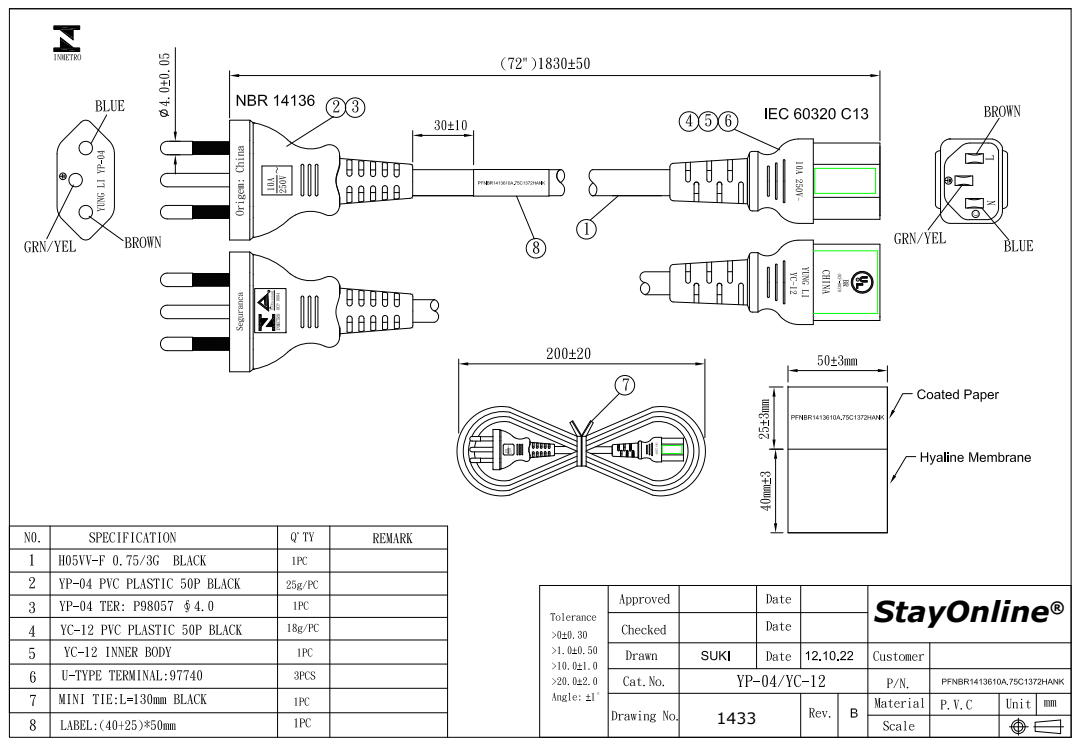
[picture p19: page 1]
StayOnline

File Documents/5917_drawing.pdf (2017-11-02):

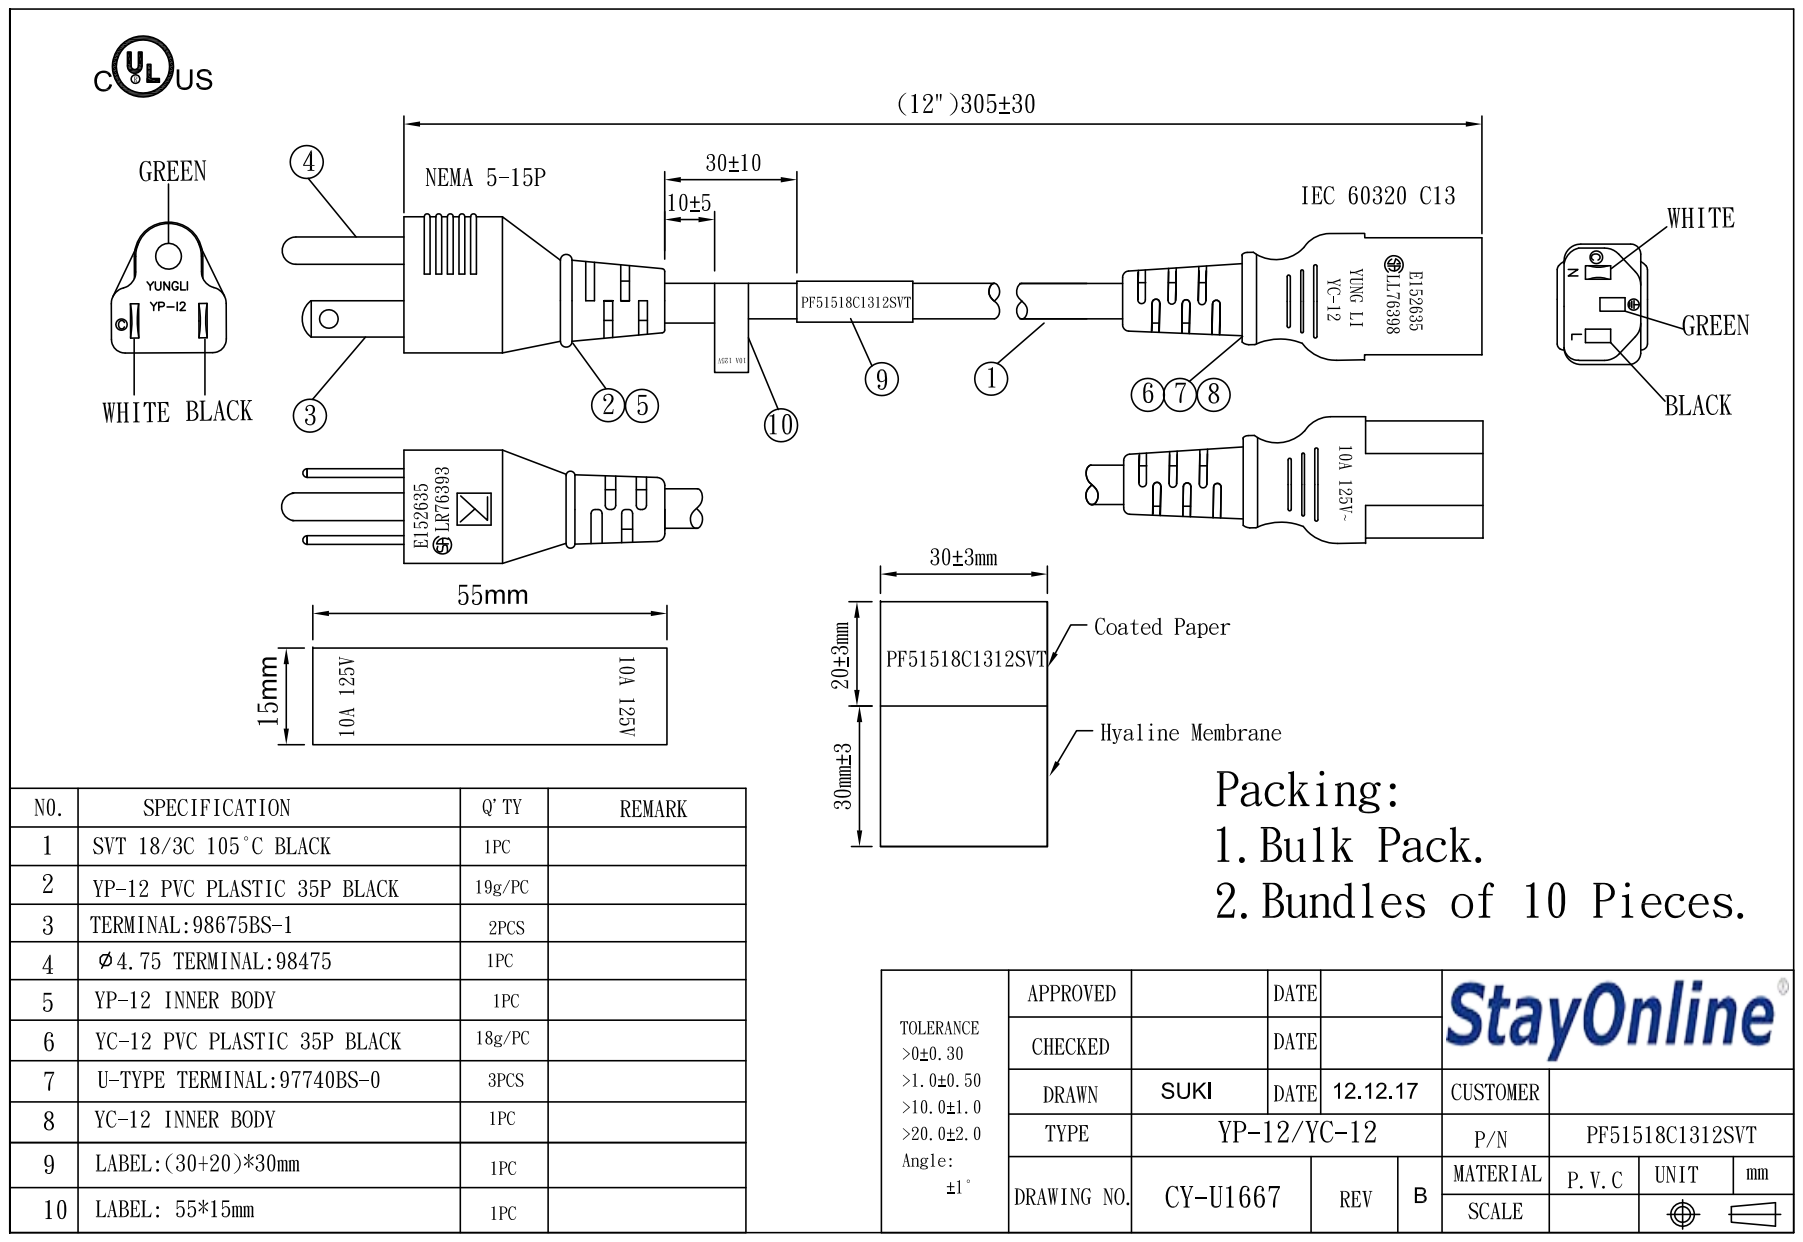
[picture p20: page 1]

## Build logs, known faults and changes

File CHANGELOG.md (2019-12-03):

# CHANGELOG
Marlon Mark I - 3D Printer, Change log

## [2.0.0] - 2019-12-03
### Tested
- Just tested new Marlin firmware version.

## [1.1.9] - 2018-08-21
### Tested
- Just tested new Marlin firmware version.

## [1.1.6] - 2017-11-15
### Changed
- Set: Motherboard to RAMPS v1.4 EFB (Extruder, Fan, Bed).
- Enable: Memory Monitoring.
- Enable: Print Counter.
- Enable: EEPROM.
- Enable: Speaker.

## [1.1.6] - 2017-11-11
### Changed
- Printer name set to "Marlon".
- Who made the changes.

## [1.1.5] - 2017-10-27
### Changed
- CoreXY.

## [1.1.5] - 2017-10-12
### Changed
- configure.sh verbose output messages.

## [1.1.5] - 2017-09-08
### Changed
- configure.sh invoke xc inside this program.

## [1.1.x] - 2017-09-07
### Added
- configure.sh version information to output string.

## [1.1.x] - 2017-09-04
### Added
- configure.sh get firmware updates on start up.

## [1.1.0-RC8] - 2017-08-22
### Added
- configure.sh verbose messages.

## [1.1.0-RC8] - 2017-02-24
### Changed
- Set: Thermistor minimum temperature to 0.

## [1.1.0-RC8] - 2017-02-22
### Changed
- Enable: Full Graphic Smart Controller.
- Enable: SD Card support.

### Changed
- Set: Printer name to "Marlin".

## 2016-01-16
### Added
- Project definition.

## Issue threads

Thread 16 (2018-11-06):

Mechanics - Back panel - Fix T-slot_90_corner

marcio-pessoa, 2018-11-06:

Closed 2018-12-27.

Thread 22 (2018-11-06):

Mechanics - Elevator - Mount

marcio-pessoa, 2018-11-06:

marcio-pessoa, 2018-11-28:
A placa usada na lateral do elevador não possui a rigidez necessária para promover a estabilidade durante o movimento. Será necessário voltar ao desenho dessa placa.

marcio-pessoa, 2018-12-27:
Aguardando peça mencionada no Issue #7 .

Closed 2020-07-17.

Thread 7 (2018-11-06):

Mechanics - Elevator - Design

marcio-pessoa, 2018-11-06:

marcio-pessoa, 2018-12-27:
Desenho concluído.

Pedi @augustorallo ver com o Pai dele (que possui habilidades superiores aos Anões de Nidavellir) se pode fazer a peça. Será épico! :-)

Closed 2018-12-27.

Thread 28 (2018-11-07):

Electronics - MSTBV - Convert from MSTBVA

marcio-pessoa, 2018-11-07:

marcio-pessoa, 2018-11-07:
Esse é o conector da RAMPS, foi necessário convertê-lo para funcionar na vertical, de tal forma que pudesse ser instalado no frame consumindo menos espaço.
A conversão consiste em meramente demover o conector e moldar os pinos de solda para encaixarem verticalmente.

Closed 2018-11-07.

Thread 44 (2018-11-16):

Electronics - Z+ endstop is now working

marcio-pessoa, 2018-11-16:
The Z+ endstop sensor is not reporting to Marlin:

```
M119
Reporting endstop status
x_min: TRIGGERED
y_min: TRIGGERED
z_min: open
ok
```

marcio-pessoa, 2018-11-16:
Problem solved enabling the following lines in `Configuration.h`:

```
#define USE_XMAX_PLUG
#define USE_YMAX_PLUG
#define USE_ZMAX_PLUG
```

The result:
```
M119
Reporting endstop status
x_min: TRIGGERED
x_max: TRIGGERED
y_min: TRIGGERED
y_max: TRIGGERED
z_min: open
z_max: open
ok
```

Closed 2018-11-16.

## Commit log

2017-11-08 Adding GT2 Timing Pulley 20T, 5mm Bore, for 6mm belt
2017-11-11 Changed Printer name set to "Marlon"
2017-11-23 Added Shaft coupler
2018-01-24 Add 'BOM.md'
2018-01-24 Tested on Marlin 1.1.8
2019-06-15 Minor updates
    [Anet_A8_removable_heat_bed.FCStd]
2019-12-03 Added Marlin as submodule
2020-05-20 Added Elevator Carriage Base 2D design
2020-05-22 finished heatbed base
2020-08-22 Marlin updated
